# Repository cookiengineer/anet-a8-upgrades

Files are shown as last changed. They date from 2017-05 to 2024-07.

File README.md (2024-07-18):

# Anet A8 Upgrade Tutorial

This repository contains all necessary upgrades for the
Anet A8 to increase its printing quality, sorted by
priority and in a form of a step-by-step-for-noobs
guide as it was a bit hard to find all the things on
the interwebz for me.

Hopefully this guide can help others upgrading their
Anet A8 and ease up the process.

## TL;DR Parts List

This is the third-party parts list that you will
need to buy to do all upgrades explained below

- 2mm/4mm PTFE (teflon) tube (min. 50cm length)
- 2.5mm GT2 timing belts (min. 200cm length)
- 2x 4mm pneumatic adapter (tube feed)
- 2x M5x50 screws
- 2x M5 self-sealing nuts
- 2x NEMA 17 stepper motors

Note: The PTFE tube needs to have inner diameter
of 2mm and outer diameter of 4mm. If you want to
use bigger filament diameters, change the pneumatic
adapter sizes accordingly.

Important: The Z-Axis stepper motors should be
replaced with stronger 17-ones, as many users
(including me) had troubles with a stuck Z-axis
motor driver that was too weak to lift the
X-carriage.

## Step-By-Step Guide

This Guide can be followed after you've already
assembled your Anet A8 3D printer.

The [installation instructions](./instructions/installation-instructions.pdf)
are also available.

The Anet A8 is delivered with varying power supplies.
If you are unsure on how to connect it, compare your
power supply with [this photo](./instructions/power-supply.jpg).

The mainboard's schematics are also available at
[this picture](./instructions/mainboard.jpg).

**IMPORTANT**: The connectors for the power cables
of the heatbed and extruder on the mainboard are of bad
quality, it is important that you connect the cables with
some space to the insulation. Otherwise your cable
insulation will overheat and burn down.

The [printing quality troubleshooting guide](./instructions/quality-troubleshooting-guide.pdf)
is also available in case some prints are deformed or broken.

----------

**1: Belt Tensioners, Belt Holders, GT2 Belts and Z-Wobble Fixes**

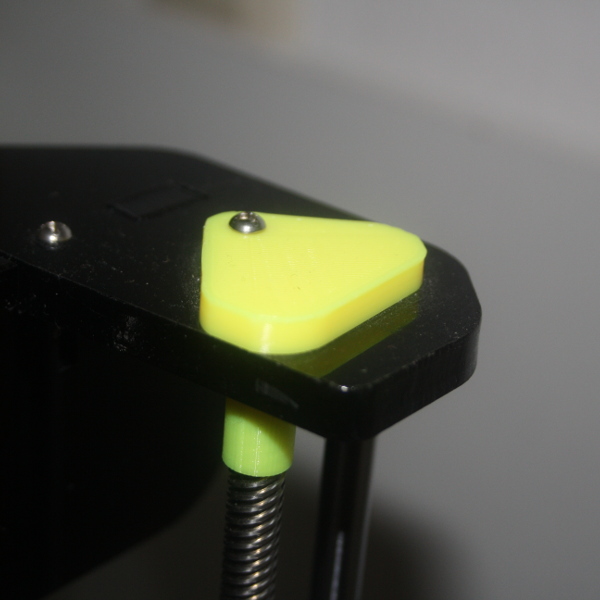
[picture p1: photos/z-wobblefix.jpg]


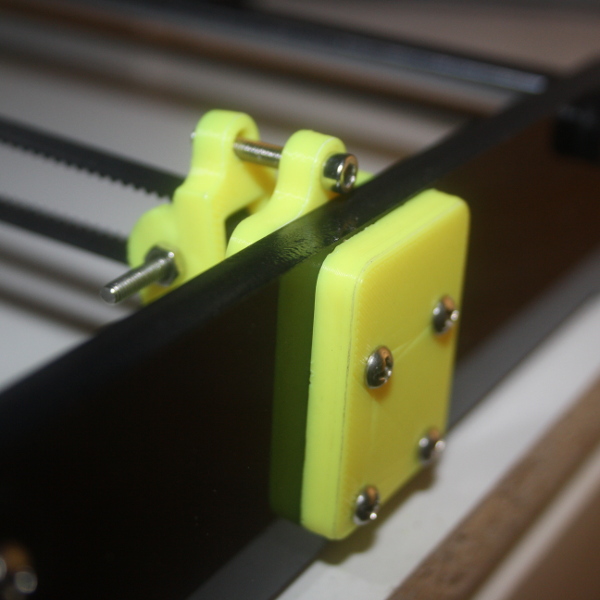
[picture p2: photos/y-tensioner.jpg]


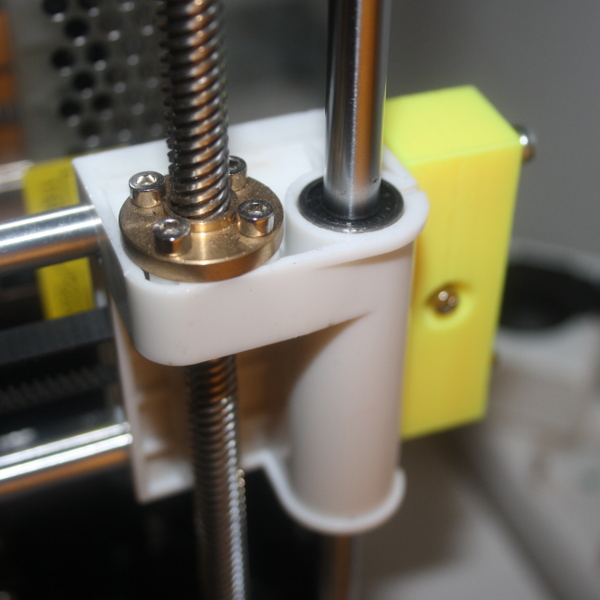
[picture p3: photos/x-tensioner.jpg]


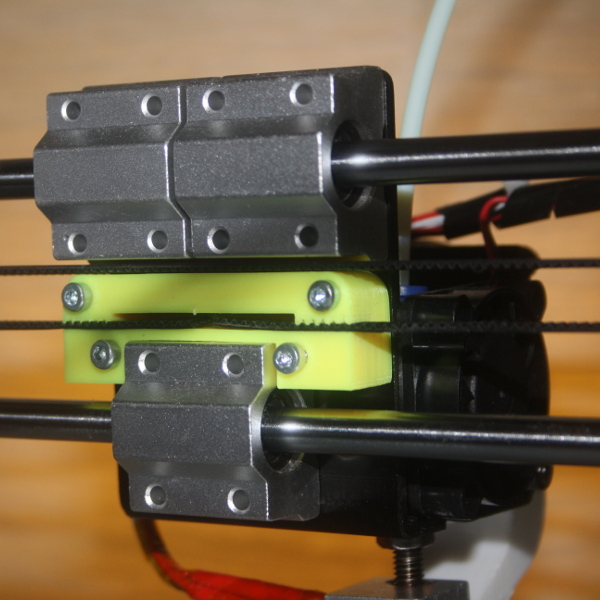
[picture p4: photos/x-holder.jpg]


If you can't use another printer, print these parts and
immediately upgrade the Anet A8 afterwards, so that later
prints will have a better quality.

Suggested print settings:

90% honeycomb infill for all prints.

* 0.12 mm layer height for x-belt holder and z wobble.
* 0.2 mm layer height for the rest.

- Print the [x-belt holder](./parts/belt-holders/x-belt_holder.stl) 1 time. 
- Print the y-belt holder [top](./parts/belt-holders/y-belt_holder-top.stl) and [bottom](./parts/belt-holders/y-belt_holder-bottom.stl) each 1 time. Su
- Print the [x-belt tensioner](./parts/belt-tensioners/x-tensioner.stl) 1 time.
- Print the y-belt [tensioner](./parts/belt-tensioners/y-tensioner.stl), [adapter](./parts/belt-tensioners/y-tensioner-adapter.stl) and [holder](./parts/belt-tensioners/y-tensioner-holder.stl) each 1 time.
- Print the [z-wobble fix](./parts/z-wobble/z-wobblefix.stl) 1 time and the [t-corner](./parts/z-wobble/t-corner.stl) 2 times.

Install the belt tensioners, the belt holders, the t-corners
and the z-wobble fixes on your Anet A8 printer.

Note that the x-tensioner requires 2 M5 screws with at
least 35mm in length with matching self-sealing nuts.
In order to have some space left for not-so-tight belts,
use the M5x50 screws there.

Make sure to use proper fiber-rubber GT2 belts, not the
plastic OEM ones that came with the printer. It is best
to buy a GT2 belt set, so that you have bigger cog wheels
that you can use for the bowden extruder upgrade :)

----------

**2: Glass Plate with Clip Holders**

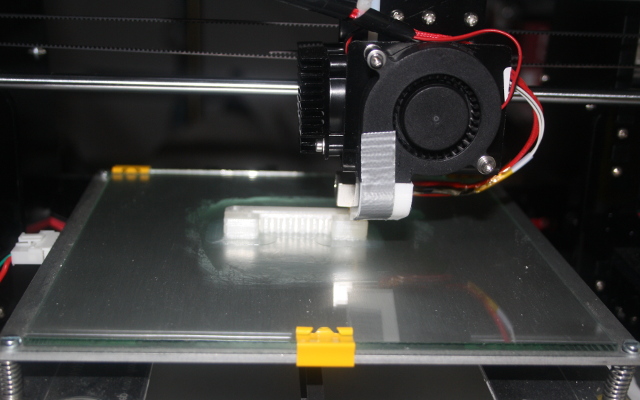
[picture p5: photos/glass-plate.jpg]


(Recommended) Install a glass plate with clip holders,
so that you don't have to use that shitty print tape.

Install the clip holders so that they don't conflict
with the `0/0/0` (Home All) position of the extruder.

When using a glass plate, it is recommended to use a
simple glue stick to make things sticky and to print
on it as the glass plate itself is too slick for the
initial layers of PLA or ABS.

Some other people often recommend to increase the
temperature, but this will cause more problems than
it solves. So just stick with the glue stick and
everything is fine, cheap and will work perfectly.

----------

**3: Level the Heatbed**

Leveling the heatbed is pain. It is recommended to level
the heatbed using a `mechanic's (water) level`. Make sure
to have a flat, leveled underground under the printer.

Afterwards follow [this instruction video](https://www.youtube.com/watch?v=O55x7B-MsE4)
to level the heatbed correctly.

Take your time; correctly leveling the heatbed is 50% of
the print quality. It's seriously important to be done
right.

----------

**4: Replace Z-Axis Stepper Motors**

The OEM stepper motors are too weak to properly lift
the X-carriage. In my case, they broke down around 10 
hours after printing, typical symptom is thatthe Z-axis 
motors make a "loud shredding noise" and/or only one is 
reacting because the Z-motor driver on the main board 
already broke down.

To avoid this, it is heavily recommended to replace the
Z-axis motors with larger ones. I suggest 48 mm NEMA 17
motors, as they are quite a bit larger than the OEM ones
but still fit well inside the frame.

There is a list of commonly used NEMA 17 motors available
from the [reprap wiki](http://reprap.org/wiki/NEMA_17_Stepper_motor).

Wiring-wise it is actually a lot of fiddle work. For me
the wiring was blue/black cross-paired and the outer two
wires being normally connected.

You have to try this out yourself, as every stepper
motor is differently wired and every stepper cable seems
to have different colors for each cable pair.

It takes a while, so grab a cup of camilla tea and stay
calm while doing it.

----------

**5: Download and Setup Cura Software**

The Cura software that comes with the USB Stick (or microSD
card) is outdated. Install the newest stable one from
[ultimaker.com](https://ultimaker.com/en/products/cura-software).

Important Note for Linux users: Pretty much all packaged
builds are totally broken, use the self-executing AppImage
from the ultimaker website. (Seriously, it even doesn't work
on Arch)

Start the Cura software, add a new printer (which is the
welcome dialog on first start).

Select `Custom` > `FDM Printer`. The detailed printer
settings are these:

```
// Printer Settings

x (width):  220mm
y (depth):  220mm
z (height): 240mm // use 235mm if heatbed has glass plate

build plate shape: rectangular
machine center:    NOT zero
heated bed:        yes

Printhead Settings

x min: 0mm
y min: 0mm
x max: 0mm
y max: 0mm

gantry height: 0mm
nozzle size:   0.4mm
```

Set the `GCode Flavor` to `RepRap (Marlin)`.

Enter the following Start GCode:

```gcode
G21            ;metric values
G90            ;absolute positioning
M82            ;set extruder to absolute mode
M107           ;start with the fan off
G28 X0 Y0      ;move X/Y to min endstops
G28 Z0         ;move Z to min endstops
G1 Z15.0 F9000 ;move the platform down 15mm
G92 E0         ;zero the extruded length
G1 F200 E3     ;extrude 3mm of feed stock
G92 E0         ;zero the extruded length again
G1 F9000
M117 Printing...
```

Enter the following End GCode:

```gcode
M104 S0                      ;extruder heater off
M140 S0                      ;bed heater off
G91                          ;relative positioning
G1 E-1 F300                  ;retract the filament to release pressure
G1 Z+0.5 E-5 X-20 Y-20 F9000 ;move Z up a bit
G28 X0 Y0                    ;move X/Y to min endstops
G90                          ;absolute positioning
G1 Y190 F9000                ;(optional) move heatbed to front
M84                          ;steppers off
```

Now go to `Settings > Profiles > Manage Profiles` and
import [this cura profile](./profiles/normal_quality.curaprofile).

It will lead to the correct settings that you need to make the
Anet A8 print awesome results.

You can verify that your Anet A8 machine is correctly set up by
comparing the [machine\_instances](./profiles/machine_instances)
folder with the one located at `~/.local/share/cura/machine_instances`.

----------

**6: Print the Calibration Cube**

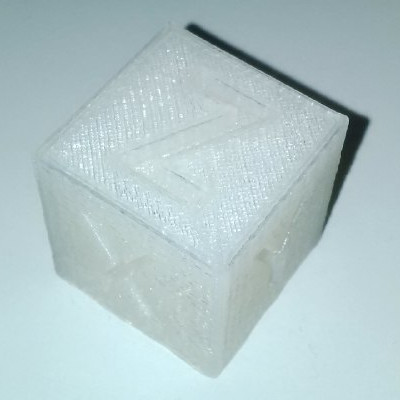
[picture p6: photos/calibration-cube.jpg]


Now it's time to test your settings. Make sure the printer
is ready, has its filament, is correctly leveled and ready
for a test run.

The test run consists of a [Calibration Cube](./calibration_cube.stl),
while setting infill to `50%` and printing it with support
structures.

If the cube is not `20mm` in all dimensions or its shape
does not look like in the picture, you probably have a not
correctly leveled heatbed and you should re-level it.

----------

**7: Upgrade the Spool Holder**

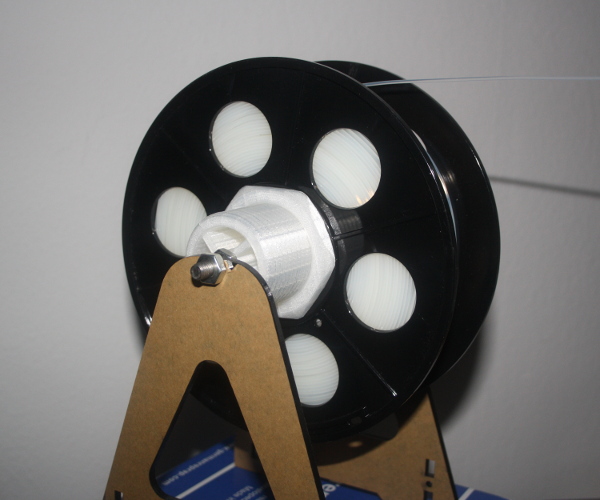
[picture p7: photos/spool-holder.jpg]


The OEM spool holder kinda sucks and does not work well
with a bowden setup due to causing more stress on the bowden
extruder than is necessary.

- Print the [spool holder bolt](./parts/spool-holder/spool-holder-bolt.stl) 1 time.
- Print the [spool holder nut](./parts/spool-holder/spool-holder-nut.stl) 1 time.

Install the spool holder afterwards. Make sure that the feeding
of the extruder motor is not hindered by other parts that are in
the way and that the filament is a straight line between spool
holder and the extruder motor.

----------

**8: Upgrade to Bowden Extruder**

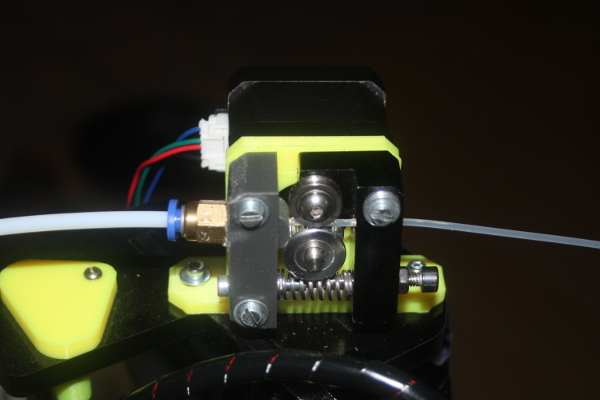
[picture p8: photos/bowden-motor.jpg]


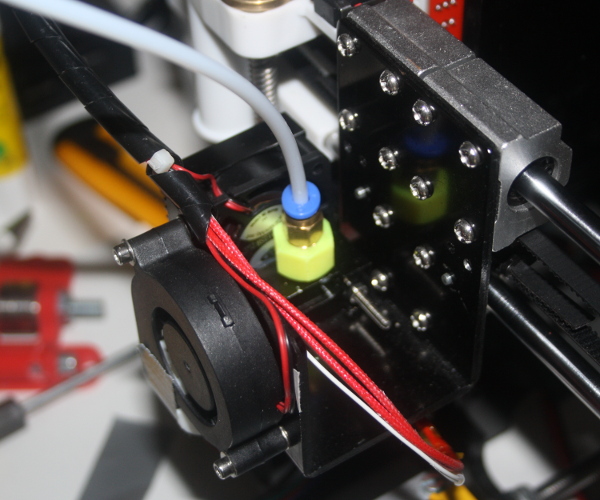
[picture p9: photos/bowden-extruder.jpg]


The standard Anet A8 setup comes with an extruder motor
mounted directly above the extruder. This causes more
weight on the X-axis that has to be moved by the X-axis
motor and belt.

The bowden extruder upgrade allows the extruder motor to be
moved atop the frame, so that it both stabilizes the frame and
allows the filament to be fed through a PTFE (teflon) tube.

- Print the [motor block](./parts/bowden-extruder/motor-block.stl) part 1 time.
- Print the [motor mount](./parts/bowden-extruder/motor-mount.stl) 1 time.
- Print the [pneumatic adapter](./parts/bowden-extruder/pneumatic-adapter.stl) 2 times (1 replacement part, you will need it).
- Print the [extruder button](./parts/bowden-extruder/extruder-button.stl) 1 time.

Install the motor parts as in the photo above, do the same for
the extruder. It is necessary to have the PTFE tube and the
pneumatic tube feeds available.

An important note here is that PTFE tube feeds have inch measurements,
not metric ones (as it's pneumatic hardware). So it is important to
buy a 3/8" tube feed (~9.51mm), as M10 (~10.18mm) would be too big to
fit the adapter. If you have an M6 thread cutter, it is recommended
to use it for the smaller side of the pneumatic adapter, so that less
stress is on the PLA (or ABS) material when being screwed into the
metal motor block on the X-carriage.

Mount the extruder motor on the top left of the printer's frame,
so that the PTFE tube-side points to the front-left direction.

Make sure that the cables and the PTFE tube don't conflict in
the whole movement area of the X-carriage.

Your printer should now look like this:

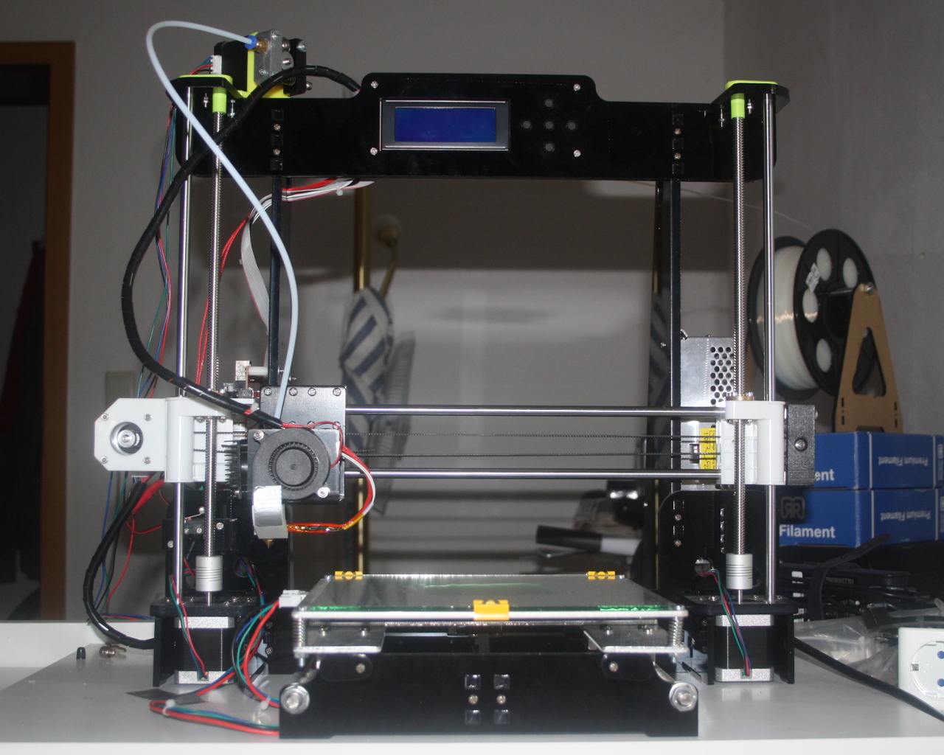
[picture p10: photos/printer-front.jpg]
printer-front


Important: The extruder motor will probably require a bigger
cog wheel, because the OEM one is a little too small to feed
the filament properly.

You can use the ones that came with the GT2 belt set that you
bought in step 1.

----------

**9: Upgrade Z-Endstop**

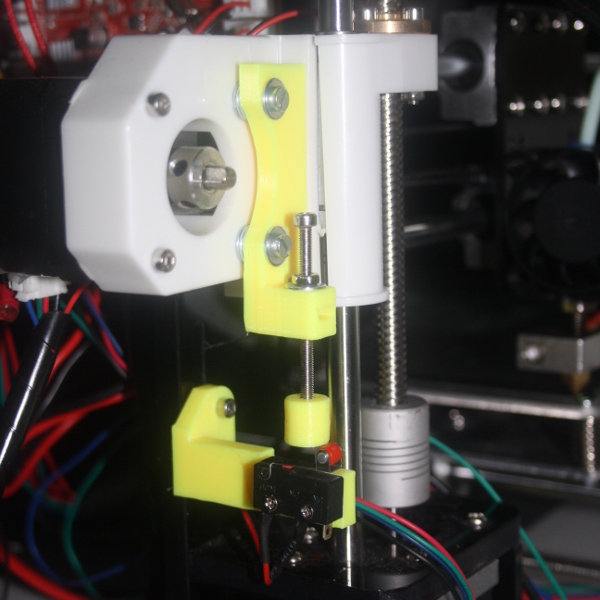
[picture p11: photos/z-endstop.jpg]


The Z-Endstop sucks hard. That's the truth, but there's a way
around it. The better endstop is adjustable, so that no matter
how your heatbed looks like, you can simply adjust one screw
without having to always recalibrate the endstop itself.

- Print the [endstop mount](./parts/z-endstop/endstop_mount.stl) 1 time.
- Print the [endstop holder](./parts/z-endstop/endstop_holder.stl) 1 time.
- Print the [endstop cap](./parts/z-endstop/endstop_cap.stl) 1 time.

Install the Z-Endstop afterwards. If you reset the position to
"Home All" in the printer's firmware menu, you can listen to the
sound of the endstop.

It has to be mounted in a way that it's directly clicking and in
the "Off" position when you move the Z-Endstop adjustment screw
by around 30deg.

Use a couple of M3 washers to adjust the distance, so that the
cap is able to hit the endstop correctly.

----------

**10: Fix the Heatbed Cable Connector**

Apparently most people build up the Anet A8 / Prusa i3 printer
by mounting the heatbed in a way that the cables of the heatbed
lead to the side and not to the back.

At first glimpse the Y-Cable Chain is a well-thought fix for
having nice clean cables. Turns out out that this causes a
burned cable connector because of too much stress.

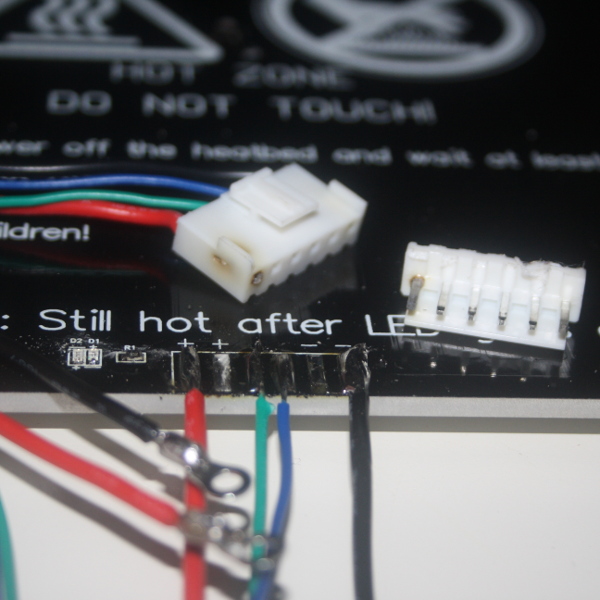
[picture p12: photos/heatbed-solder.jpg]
heatbed-solder


It is recommended to re-solder the heatbed, and to mount the
heatbed in a way that the cables lead to the back, and NOT to
the side - so that the cables and soldered connections don't
have too much stress on them.

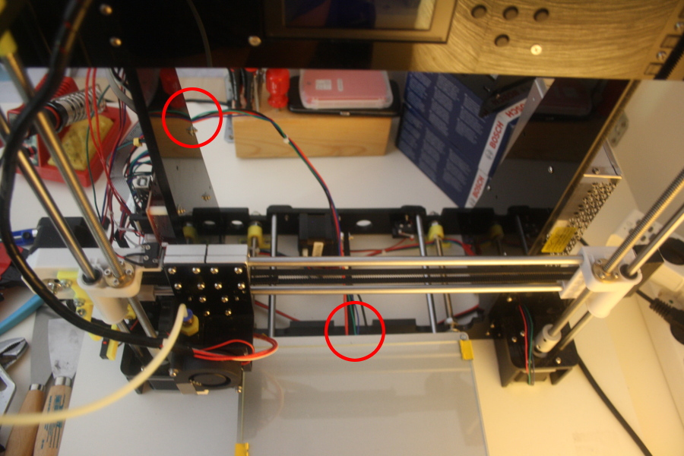
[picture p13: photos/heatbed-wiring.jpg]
heatbed-wiring


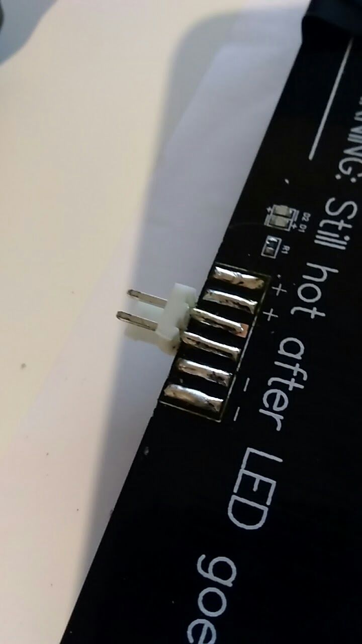
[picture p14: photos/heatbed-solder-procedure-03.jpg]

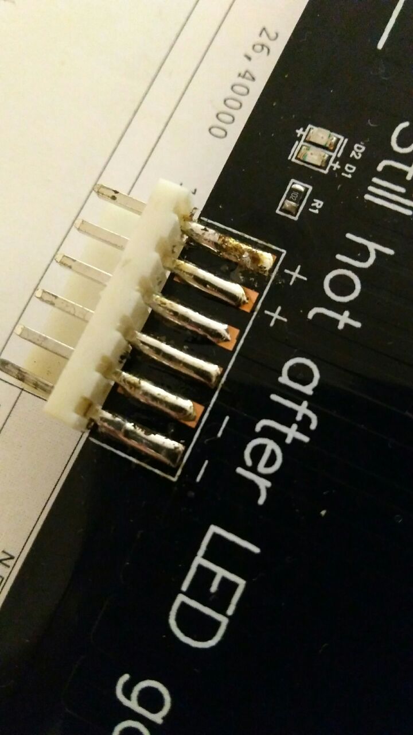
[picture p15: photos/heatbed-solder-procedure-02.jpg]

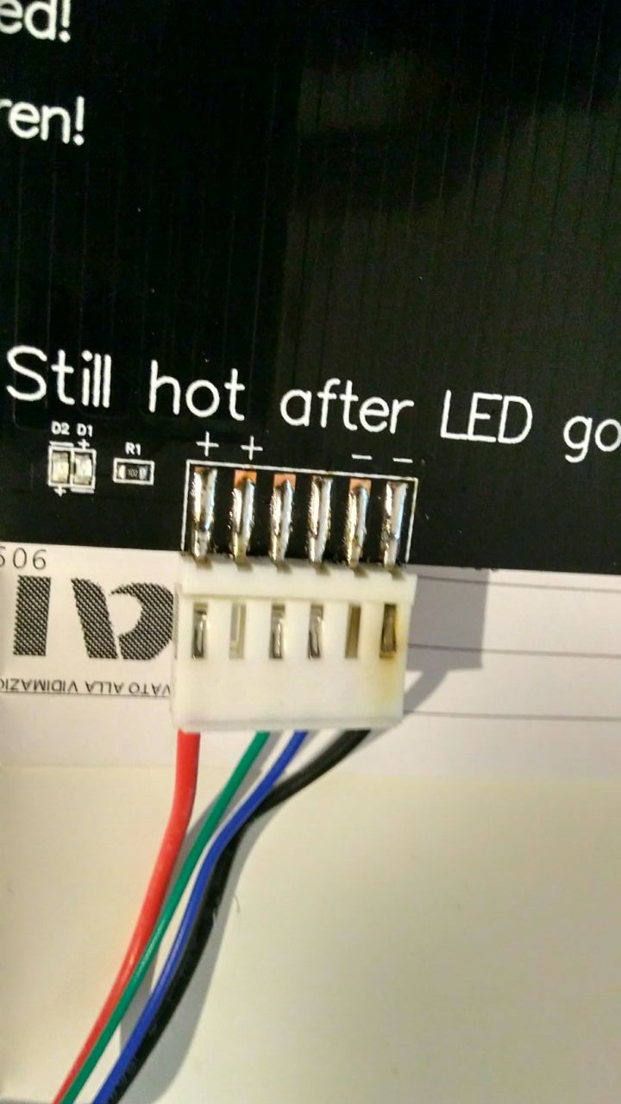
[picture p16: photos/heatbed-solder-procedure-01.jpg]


At first your heatbed will stop working, and the heat will stop at the connector, eventually leading to a burnt connector or worse - [it's a fire hazard](http://forums.reprap.org/read.php?392,493405).
The procedure is fairly simple, even if you are new to soldering. Just be patient and remove any excess solder you may use.
If the old solder doesn't come off, put a bit of new solder on it and it will melt immediately.

You can try removing the wires and pulling the connector with pliers, it will come off with a bit of force. If you desolder and remove the outer pins you can still use a piece of the original connector - cut to fit - for the thermistor.

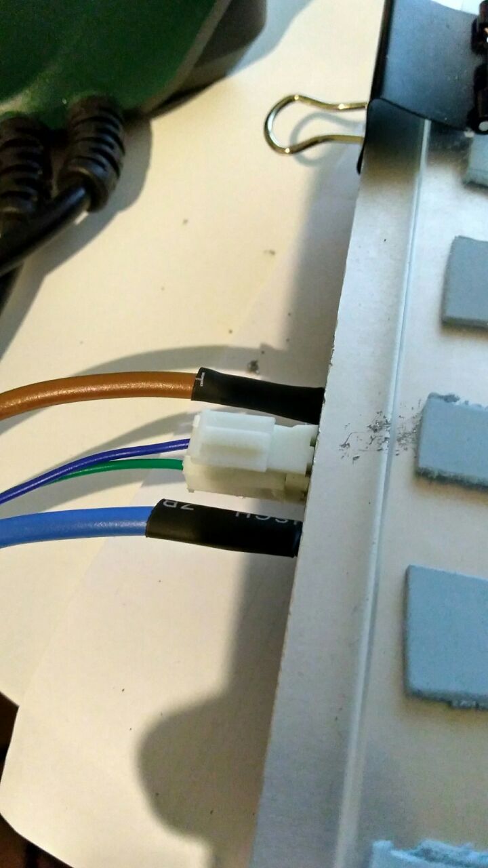
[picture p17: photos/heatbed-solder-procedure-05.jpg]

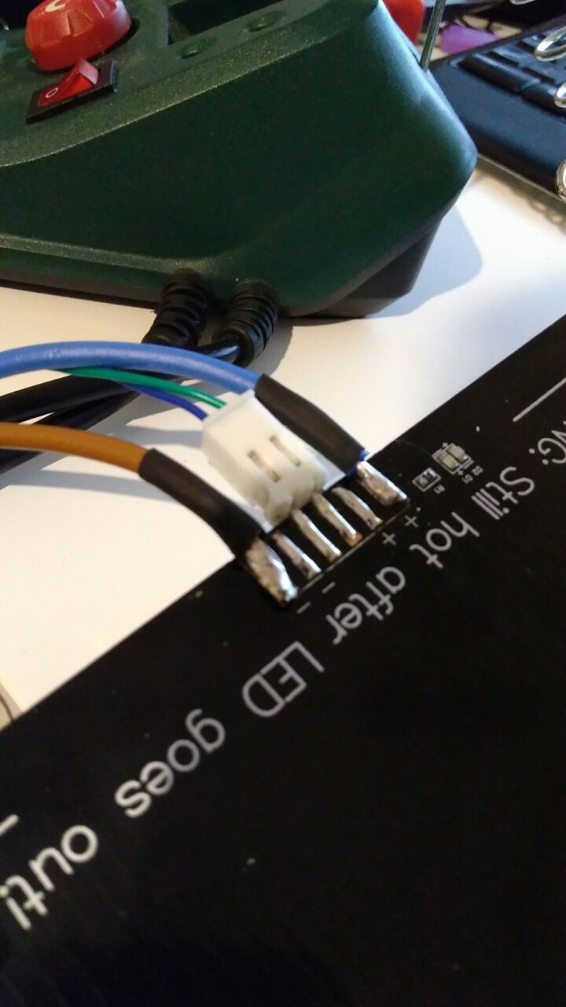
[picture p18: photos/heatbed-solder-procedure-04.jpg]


You should use an higher-gauge wire to connect the heatbed, the one that comes with the printer is too thin to carry the 10A used by the bed. A thicker cable means that the wire will stay colder when transferring current.

Remember to insert heat-shrink tubing before soldering (keep it distant from the ends or it will shrink immediately) and put it between the wire and the metal frame of the bed. It shouldn't be an issue if the wire touches the coating at the bottom of the heatbed, but it's better to keep them separated.

**Do not connect both** the + or - pins, the bed will be able to take up to 20A from the motherboard, leading to a burnt motherboard.

----------

**11: Upgrade Frame Braces**

Under heavy load the frame of the Anet A8 could potentially
crack the acryl plates. But don't worry, there's a fix for
that.

If you have placed the Anet A8 on a wooden plate, it is also
better to mount it using the threaded frame holders.

- Print out the [rear frame](./parts/frame-braces/frame-rear.stl) 1 time.
- Print out the [threaded frame holder](./parts/frame-braces/frame-holder.stl) 6 times.

Install the rear frame and the threaded frame holders. The
frame holders are best mounted on each side of the acryl
frame, so that the acryl frame has less stress on it
afterwards.

Use wood screws to mount the frame holders and at least M4
screws to mount the rear frame.

**XX: X-Axis Rework**

This is currently work-in-progress. The X-Axis rework can
be found in the [./parts/x-axis](./parts/x-axis) folder and
it contains a modified X-motor mount with the integrated
adjustable Z-endstop and adjustable X-tensioner.

When this reworked X-Axis proves stable, I will replace the
previous steps accordingly.

## Firmwares

Currently I run the stock OEM Anet A8 mainboard and the stock
firmware with my Bowden setup. This works perfectly so far,
but in case I switch to RAMPS in future, I put the firmware
in the [./firmwares](./firmwares) folder.

## Problems / Suggestions?

If you have suggestions or problems of any kind; feel free
to open up an issue so that I can improve this guide!

Don't forget to give a star if you liked it ;)

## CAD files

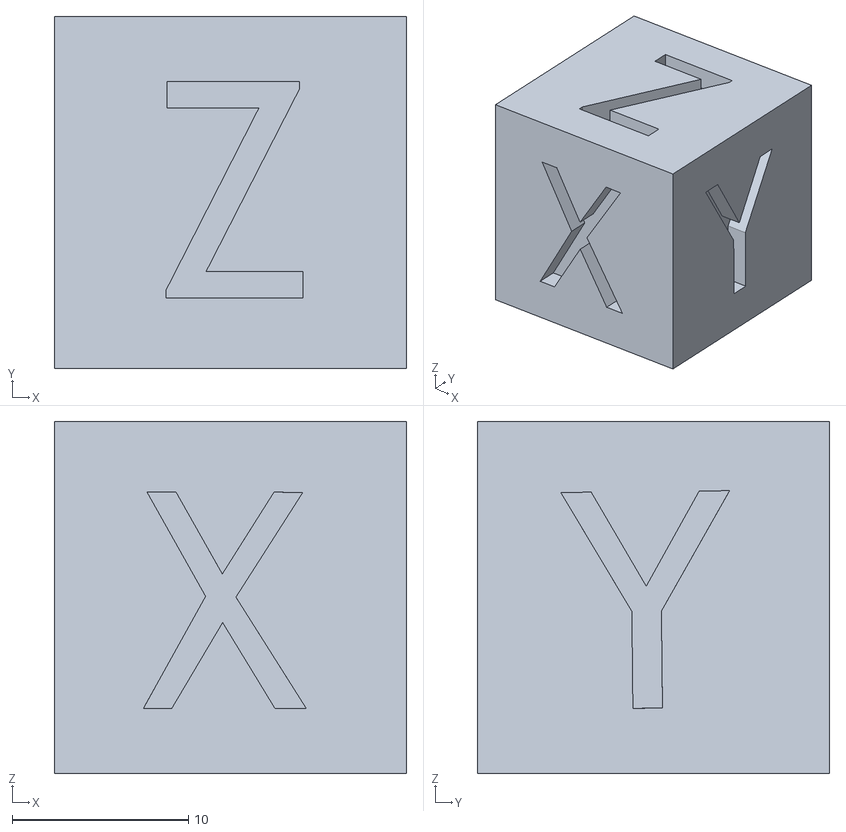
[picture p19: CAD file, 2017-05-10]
calibration_cube.stl
20.0 x 20.0 x 20.0

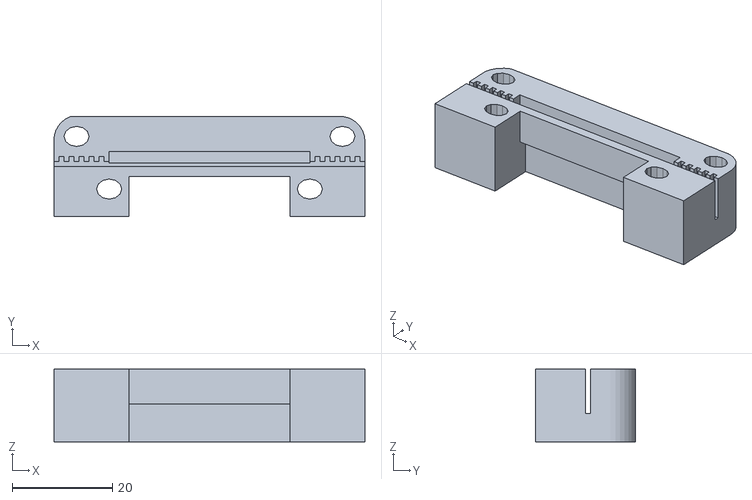
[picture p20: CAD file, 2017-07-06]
parts/belt-holders/x-belt_holder.stl
62.0 x 20.0 x 14.5

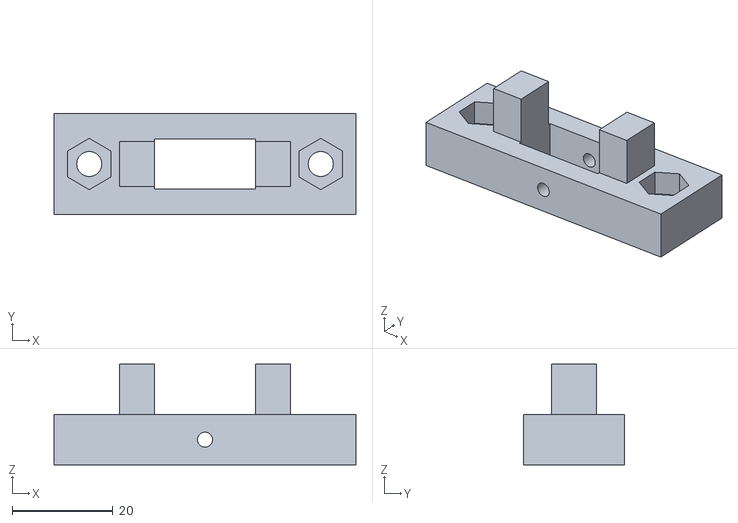
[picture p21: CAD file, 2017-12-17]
parts/belt-tensioners/x-tensioner.stl
60.0 x 20.0 x 20.0

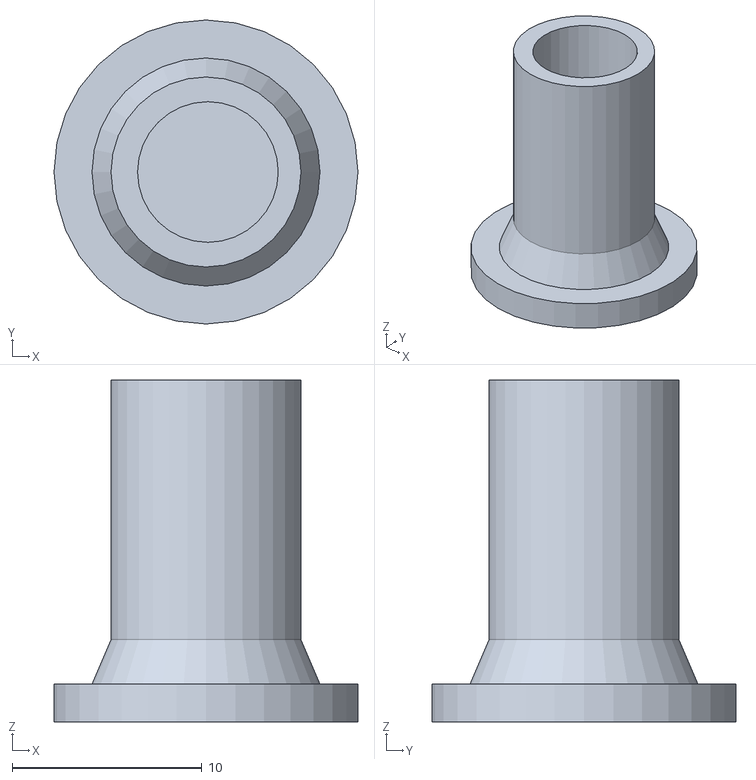
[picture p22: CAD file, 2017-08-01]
parts/bowden-extruder/extruder-button.stl
16.0 x 16.0 x 18.0

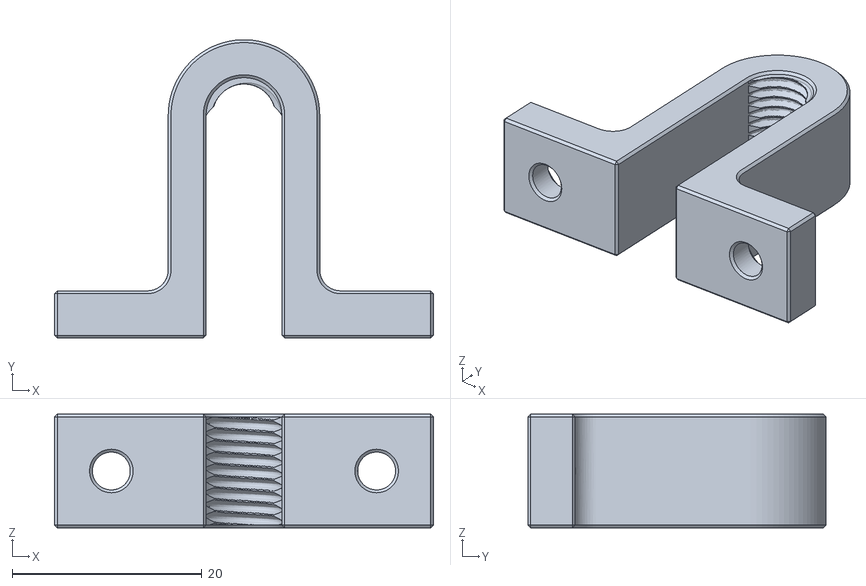
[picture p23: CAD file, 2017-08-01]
parts/frame-braces/frame-holder.stl
40.0 x 31.5 x 12.0

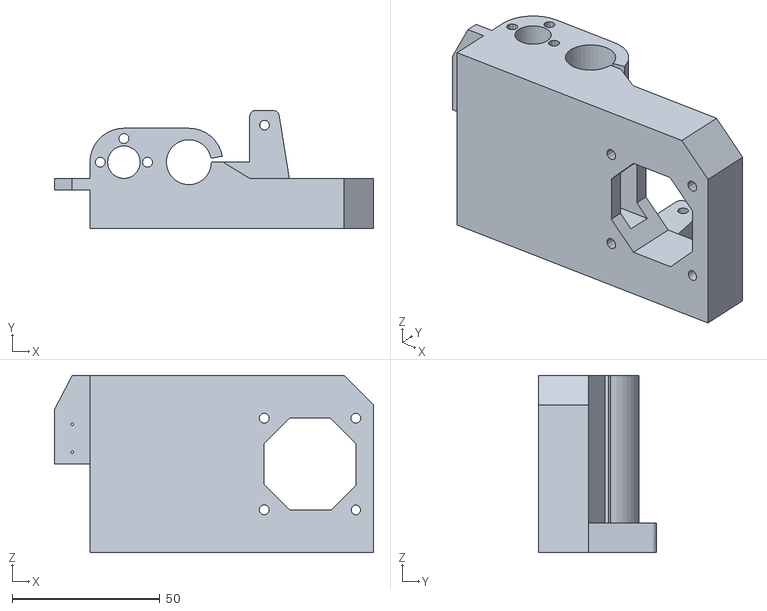
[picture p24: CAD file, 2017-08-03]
parts/x-axis/x-motor-mount.stl
108.0 x 40.0 x 60.0

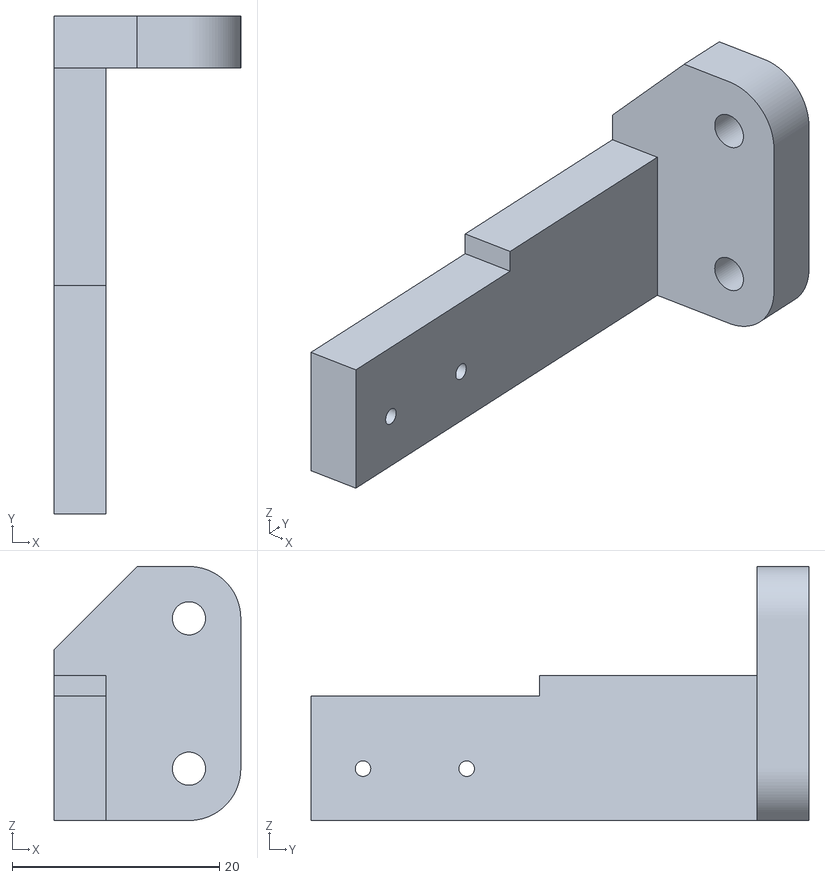
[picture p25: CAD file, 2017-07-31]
parts/z-endstop/endstop_holder.stl
18.0 x 48.0 x 24.5

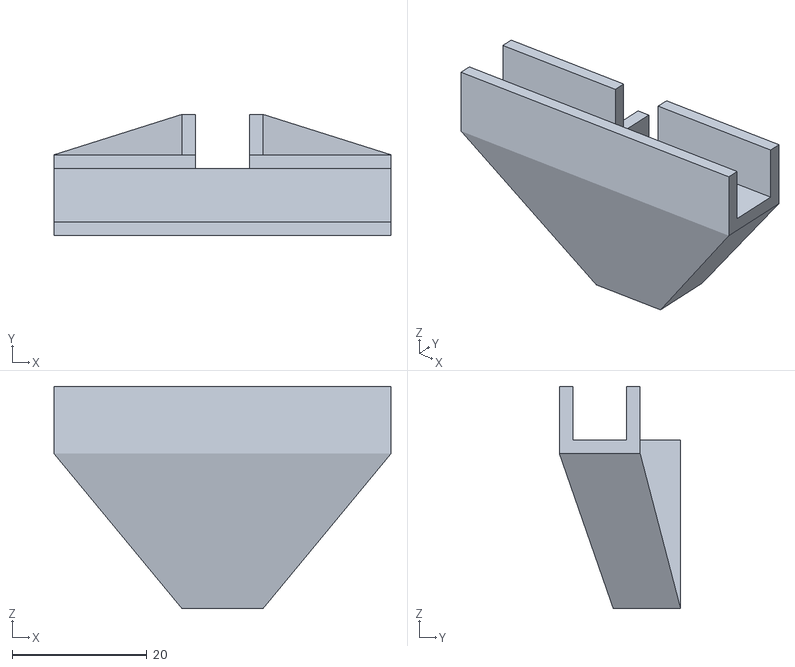
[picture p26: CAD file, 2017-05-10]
parts/z-wobble/t-corner.stl
50.0 x 18.0 x 33.0

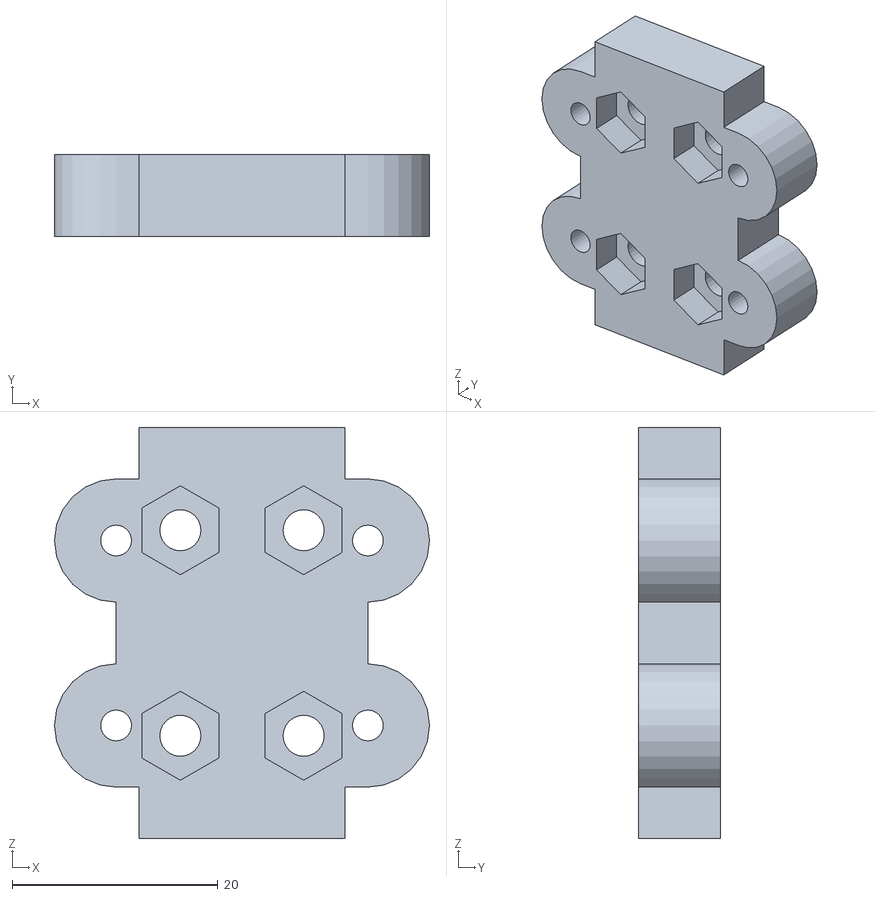
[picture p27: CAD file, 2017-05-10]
parts/belt-holders/y-belt_holder-bottom.stl
36.5 x 8.00 x 40.0

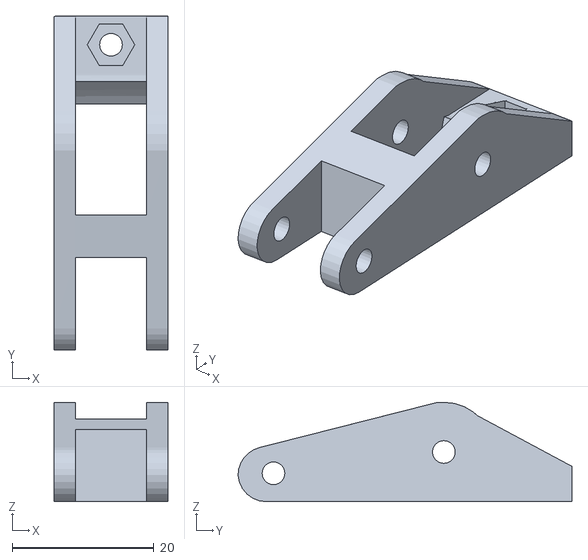
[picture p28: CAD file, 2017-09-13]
parts/belt-tensioners/y-tensioner.stl
16.0 x 47.0 x 14.0

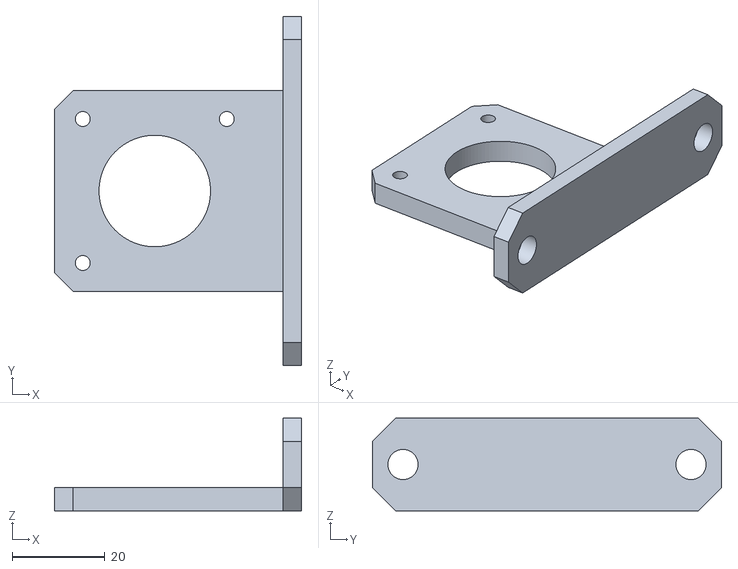
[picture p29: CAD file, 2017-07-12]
parts/bowden-extruder/motor-mount.stl
53.2 x 75.2 x 20.0

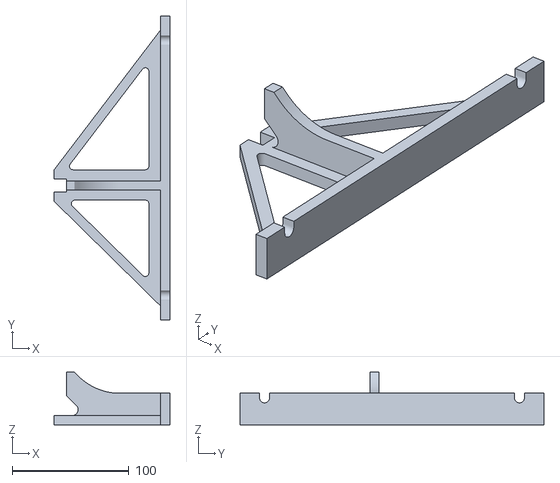
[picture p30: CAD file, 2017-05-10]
parts/frame-braces/frame-rear.stl
99.0 x 260.0 x 45.0

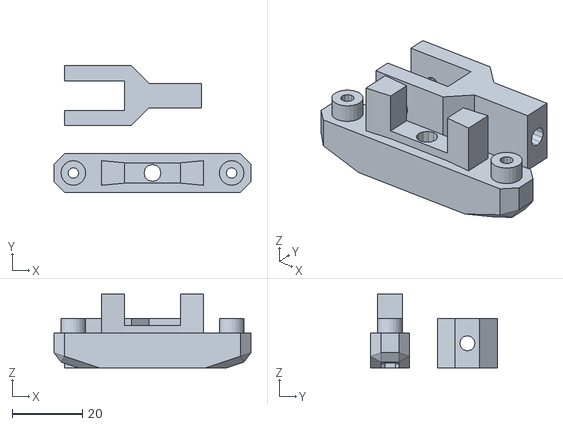
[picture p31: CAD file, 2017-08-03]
parts/x-axis/x-idler-tensioner.stl
56.0 x 36.0 x 21.0

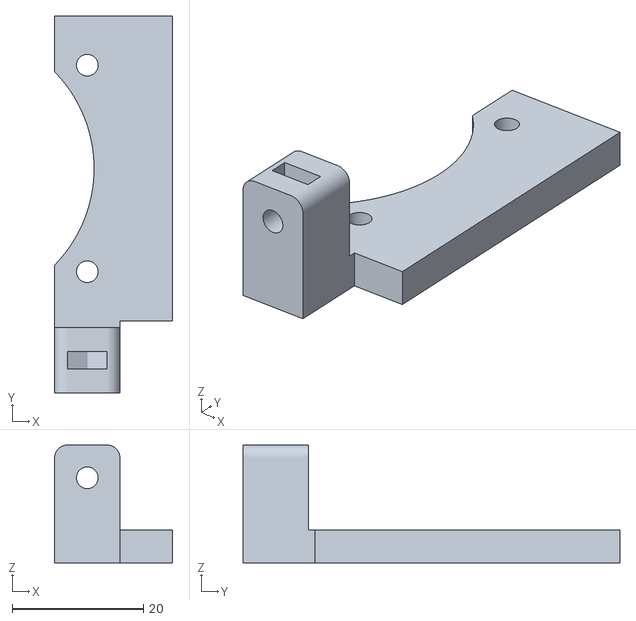
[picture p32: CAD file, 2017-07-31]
parts/z-endstop/endstop_mount.stl
18.0 x 57.5 x 18.0

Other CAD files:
parts/z-wobble/z-wobblefix.stl
parts/belt-holders/y-belt_holder-top.stl
parts/belt-tensioners/y-tensioner-adapter.stl
parts/bowden-extruder/motor-block.stl
parts/belt-tensioners/y-tensioner-holder.stl
parts/bowden-extruder/pneumatic-adapter.stl
parts/spool-holder/spool-holder-bolt.stl
parts/spool-holder/spool-holder-nut.stl
parts/x-axis/x-idler.stl
parts/z-endstop/endstop_cap.stl

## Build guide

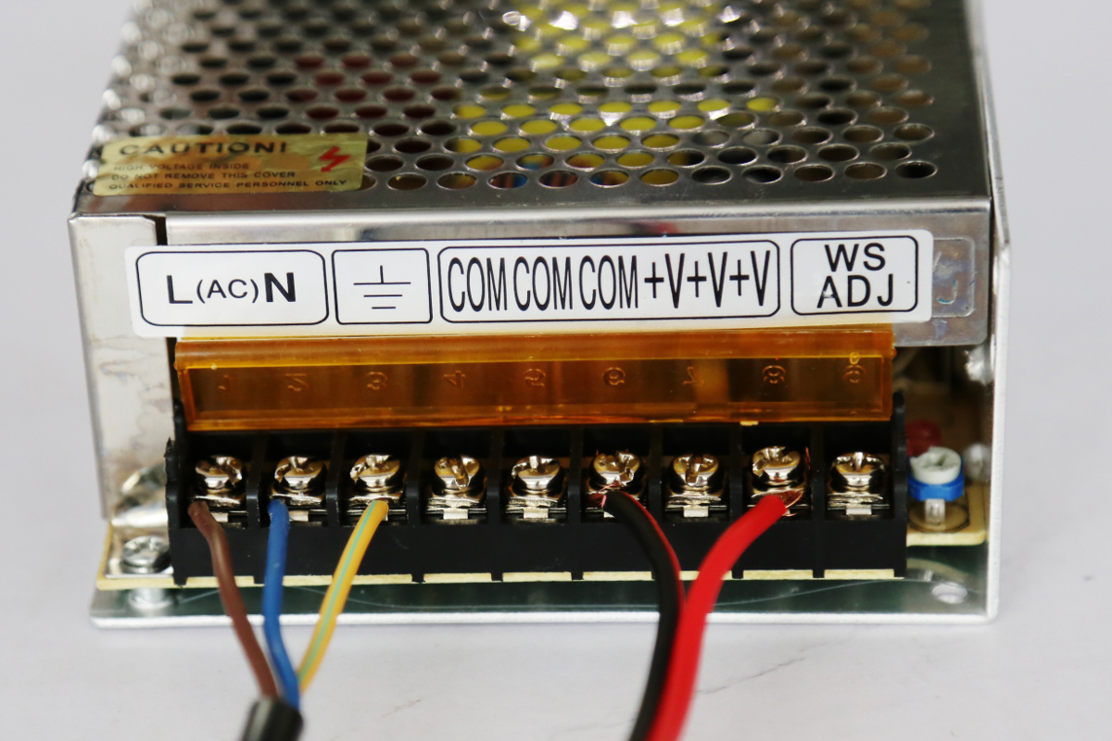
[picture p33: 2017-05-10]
instructions/power-supply.jpg

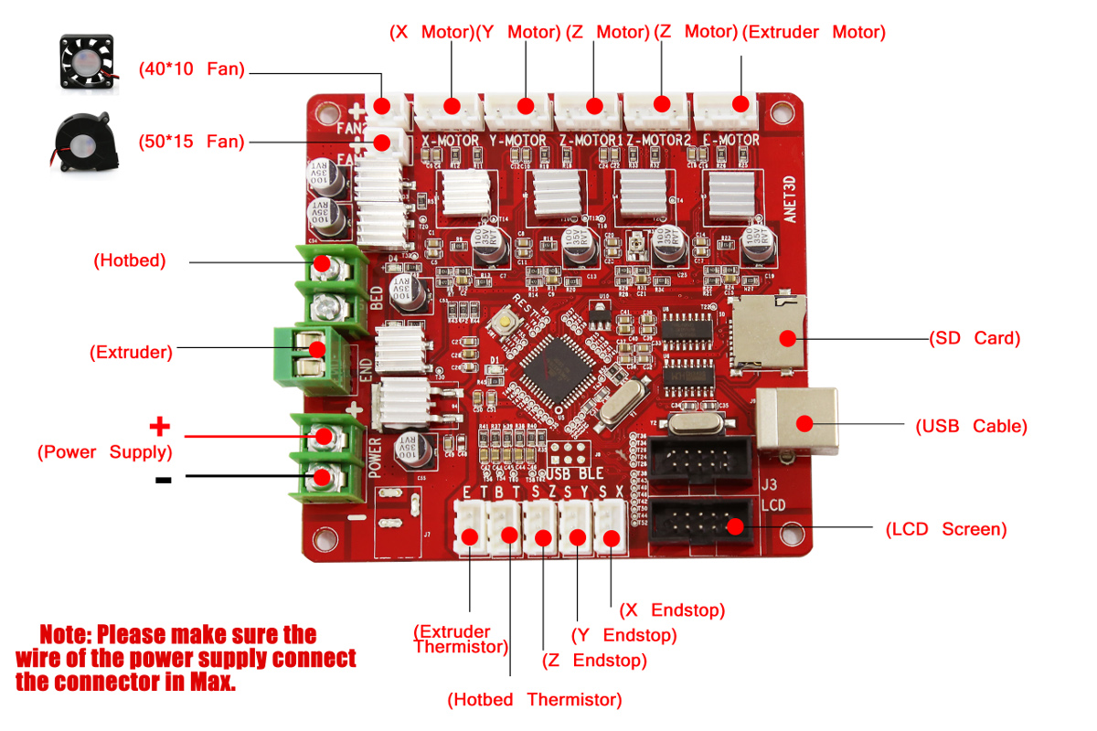
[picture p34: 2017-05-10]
instructions/mainboard.jpg

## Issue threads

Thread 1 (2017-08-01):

Highest priority: electronics safety upgrades

probonopd, 2017-08-01:
Please explain electronics safety upgrades so that the Anet A8 cannot burn the house.

* PSU mounting issue https://www.thingiverse.com/groups/sunhokey-3d-printer-owners/topic:2469
* For all cables, use ferrules before connecting to the mainboard (some say to use a mosfet) https://www.thingiverse.com/groups/anet-a8-prusa-i3/topic:12332
* Burning connectors https://m.facebook.com/groups/1068531466501015?view=permalink&id=1322694251084734&p=0
* Burning power supply https://www.reddit.com/r/3Dprinting/comments/5c8ueq/anet_a8_burns_out_the_power_supply/

and so on. This should be the most important upgrades before everything else.

cookiengineer, 2017-08-02:
I double-checked with my printer and the instructions of the Anet A8 sold by gearbest.
I cannot verify the PSU and mainboard mounting issues, but I know that the connectors of the heatbed are of bad quality and the wires have to be connected in a way that the insulation has no contact (otherwise the cable insulation will overheat).

Regarding the PSU: The short M3 screws have no contact with the 12V rail inside the PSU, I opened the PSU, measured with a volt meter and verified this. However, I removed the plastic film of the PSU when assembling the printer. I guess a mention of that wouldn't hurt.

The power drainage from the NEMA14 steppers on the Z-axis were a problem for me and I would guess a MOSFET would've helped here to prevent my Z-axis driver from burning through. However, the NEMA17 ones work perfectly without issues and the mainboard has much more reserve in manners of overvolting.

Do you have more sources on this? Are those really not user-specific assembly problems?

probonopd, 2017-08-02:
Thanks @cookiengineer. I don't have more information, just what I found in a quick web search because I keep hearing horror stories of this printer being so dangerous.

cookiengineer, 2017-08-06:
Ironically my heatbed connector burned through yesterday. I replaced the Y-Cable Chain step with the proper re-solder heatbed connector / proper wiring one.

Just thought I let you know. (Leaving this issue open until I added the necessary explanation steps for PSU).

probonopd, 2017-08-06:
Still think it would be useful to explain what "proper" is and where to get "proper" parts and do "proper" soldering. :-)

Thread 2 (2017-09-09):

Bowden stl files missing

drross, 2017-09-09:
Can you reupload the files for the bowden motor block and pneumatic adapter? I've already printed the mount and button. Thank you for the awesome write up!

cookiengineer, 2017-09-11:
You can reuse the motor block parts from the OEM Anet. The bowden upgrade only requires these parts:

- The tube feed side aka motor block (because the other one stays on the carriage)
- The motor block mount
- The bowden adapter aka pneumatic adapter (tube feed opposite), which is screwed inside the previously used motor extrusion side.

All parts are in here, the button is obviously optional :)

https://github.com/cookiengineer/anet-a8-upgrades/tree/master/parts/bowden-extruder

Let me know if that cleared things up for you.

cookiengineer, 2017-09-11:
Take this picture:

- motor block mount is yellow
- motor block part is grey
- OEM (metal part) is black

https://github.com/cookiengineer/anet-a8-upgrades/blob/master/photos/bowden-motor.jpg

Closed 2017-09-17.

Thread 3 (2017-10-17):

More information about bowden

dennisrosa, 2017-10-17:
May you explain how to use the original extruder as bowden ?
Do you use e3d hotend ? tks

dennisrosa, 2017-10-17:
I am so sorry. I find another issue explain that.

Closed 2017-10-17.

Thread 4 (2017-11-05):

4mm pneumatic adapter

jsmithgmail, 2017-11-05:
Hi, this is a great tutorial.  What size thread is needed for the adapter, is it M6?

Will this adapter work?

https://www.amazon.com/Witbot-Straight-Fitting-Connector-Printer/dp/B01NANKRTD

cookiengineer, 2017-12-04:
The small side of the pneumatic adapter is meant to fit into the motor block's hole where the extruder is screwed up in, too. The small diameter is 6mm (M6) while the bigger diameter is around ~9.5mm; but those are imperial measurements (as is all pneumatic tube stuff) so it is more likely sold as 3/8" (3/8 * 25.4 is 9.51mm).

cookiengineer, 2017-12-20:
Added a note for this into the README, so that others don't have the same problem.

Closed 2017-12-20.

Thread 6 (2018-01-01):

Stl files

zwarder, 2018-01-01:
Hi some of your files x-belt_holder / z-wobblefix do not open in cura.
Reports them as invalid file

cookiengineer, 2018-01-26:
Did you download them via the "RAW" button on github? If you download the link via "save as..." from the README file, you will end up getting the HTML preview file.

I'm mostly using cura as a slicer, so the STL files should work there. I'm still using cura 3.0.3 though.

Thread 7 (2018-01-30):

OEM_firmware.hex fries the bootloader

hashashin, 2018-01-30:
Hi, after flashing the hex, avrdude was unable to verify it and the board will not accept usb flashing anymore.
The printer works fine and the firmware was actually flashed. So I assume there's a problem with the bootloader being overwritten by your hex in some way.
The solution for me was to reflash the bootloader to set the fuses (was in stock but decided to go for optiboot, no need to set the fuses if the same bootloader it's used in the hex) and then combine the oem hex with the bootloader and flash it.
To avoid this in first place I've created 2 hex files: oem firm + stock bootloader and oem +optiboot. So if I've to reflash, it will not messup the bootloader again :)
[mergedfirmwares.zip](https://github.com/cookiengineer/anet-a8-upgrades/files/1678759/mergedfirmwares.zip)

Salud.

PD: sorry for my poor english.

cookiengineer, 2018-01-30:
Thanks for the hint!

Which version of the Anet board do you have?

Does the LCD screen show a percentage of how far the print currently has progressed? Does it have the detailed movements menu for quick home and the extruder menu to push out filament manually?

hashashin, 2018-01-30:
I've received it some days ago, as far I can remember (switched firmware again) it was showing the % of the print and does have the menu ( I used it to charge the filament). In the board it's printed "v1-5". Also In the bootscreen shows "A8" in the second line, the firmware you can download from the manufacturer was "A8-S", which bothered me. That's why I tried yours, which I assumed was readed directly from the micro with avrdude via isp (my fault don't doing that myself :\ ).

Salud.

cookiengineer, 2018-01-30:
Damn, so that probably means that the firmware that I uploaded is only compatible with the v1.4 (which is the version on my board) and not with v1.5.

Is your firmware based on repetier or the OEM one that I provided? Did you do a test print with your modified version with the optiboot bootloader and did it work G-Code wise?

cookiengineer, 2018-01-30:
I also checked the known resources, but there hasn't been any update (yet) regarding the newer board:

- https://3dprint.wiki/reprap/anet/a8
- http://anet3d.en.made-in-china.com/company-Shenzhen-Anet-Technology-Co-Ltd-.html

On my printer, I decided to meanwhile just use marlin (v2), because it was easier. Maybe it's better to just provide marlin as a failsafe alternative rather than messing with the OEM binaries to get them to boot properly :-/

hashashin, 2018-01-30:
Now has repetier, but I made prints with your binary+optiboot and all was ok.

Salud.

hashashin, 2018-01-30:
It's a shame that Anet didn't provide the source of the firmware, which I suspect it's repetier based...

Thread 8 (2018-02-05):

Print settings for upgrade parts

loidor, 2018-02-05:
Not a biggie, but it would be super with some print settings suggestions for the upgrade parts.

Most of them prints all right on a stock A8 with 0.2 layer height and 60mm/s speed, but I needed to lower the speed to 30mm/s on the X belt holder, and add a brim on the T corners in order for the thin parts to stay proper in place (that might be on me though, since I'm using PEI rather than the shipped painter's tape).

cookiengineer, 2018-02-05:
Phew, not sure what I used back then, but I would print the smaller parts with 0.12mm precision and the bigger ones with 0.2mm. Typically I use tetrahedron / octagon infill at 90% and default speed settings and they worked fine in the past.

Did you replace the belts with better ones or did you use the shitty OEM plastic ones?

loidor, 2018-02-06:
I got proper fiber glass reinforced ones.

Guess 0.12 would've worked even better than lower speed. Why not 0.1?For infill I used rectilinear at 80. Pretty much the same as honeycomb at 90, I believe.

cookiengineer, 2018-02-06:
The stepper motors of the Anet can only vary in 0.4mm because they are not more precise in their degrees that they can do technically speaking, so 0.4, 0.8, 0.12, 0.24 etc. pp. is only possible, as 0.4 is the actual measurement of a single step in Z-direction.

loidor, 2018-02-06:
Ah! Didn't know that.

Speaking of motors, although they're small they're still nema 17. There's a 5mm difference in the hole spacing, so 14s wouldn't fit the same holes as 17s :)

Do you want me to post a pull request with the edits? If so, I'll also measure what the max size of Z axis motors would be.

cookiengineer, 2018-02-06:
Yes, I'd love to merge your changes in.

cookiengineer, 2018-02-09:
Saw the PR, merged in. Thanks much!

Closed 2018-02-09.

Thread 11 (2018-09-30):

Mentioning both M5x30 and M5x35 screws

jokogr, 2018-09-30:
In the parts list M5x30 screws are being mentioned, while Section 1 mentions M5x35 screws. I guess both are equally fit since they are just here to tense the x-belt, but it could create some confusion to readers.

cookiengineer, 2018-09-30:
Yes, you are right. I should mention that the x35 is the minimum length, so you can use x50 there as length (that's my setup).

cookiengineer, 2018-09-30:
Fixed it. Reopen if it's still unclear :)

jokogr, 2018-09-30:
Thanks for clearing this out, I had ordered M5x30 screws, I should get x50 ones :unamused:

Closed 2018-09-30.

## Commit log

2017-05-10 :snowflake: Initial commit
    [calibration_cube.stl, chain_x4.stl, chainbridge.stl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]
2017-07-06 :rocket: Better X-Tensioner that does not break
    [x-tensioner.stl]
2017-07-06 :rocket: Better X-Holder that does not break
    [x-belt_holder.stl]
2017-07-12 :rocket: Bowden Upgrade and Spool-Holder
    [chain_x4.stl, chainbridge.stl, clip_end.stl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]
2017-07-12 :bug: Fixes, NEMA17 stepper motors mentioned
2017-07-31 :rocket: Z-Endstop
    [endstop_cap.stl, endstop_holder.stl, endstop_mount.stl]
2017-08-01 :rocket: Frame Holder and better X-Tensioner
    [extruder-button.stl, frame-holder.stl, x-tensioner.stl]
2017-08-03 :snowflake: Better Y Tensioner
    [y-plate.stl, y-screw.stl, y-tensioner-adapter.stl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]
2017-08-03 :snowflake: Prototypical X-Axis rework
    [x-idler-tensioner.stl, x-idler.stl, x-motor-mount.stl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]
2017-08-03 :bug: Fixes
    [x-motor-mount.stl]
2017-08-06 :bug: Remove Y-Chain because it broke heatbed connectors
    [chain_x4.stl, frame_mount.stl, hotbed_mount.stl]
2017-08-06 :bug: Missing photos for X-tensioner and Z-wobblefix
2017-08-30 :bug: Fix for Y-Tensioner
    [y-tensioner.stl]
2017-09-13 :bug: Machine Profile
    [Anet+A8.stack.cfg]
2017-12-01 :bug: Fix for X-Tensioner
    [x-tensioner.stl]
2017-12-05 Burnt connector and a bunch of soldering photos
2017-12-17 :rocket: X-Tensioner
    [x-tensioner.stl]
2018-02-06 Added suggested printer settings and more information about Z-axis motors.
